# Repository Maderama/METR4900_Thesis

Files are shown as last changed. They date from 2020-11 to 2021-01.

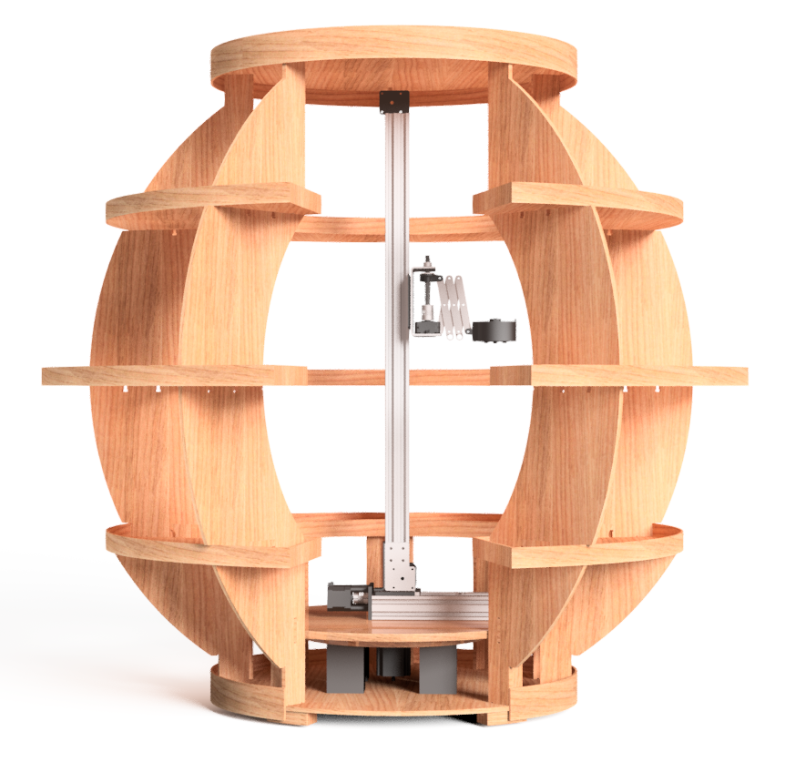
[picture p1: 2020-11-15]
CAD Model/Mechanical Drawings/Renders/FrontandSide.png

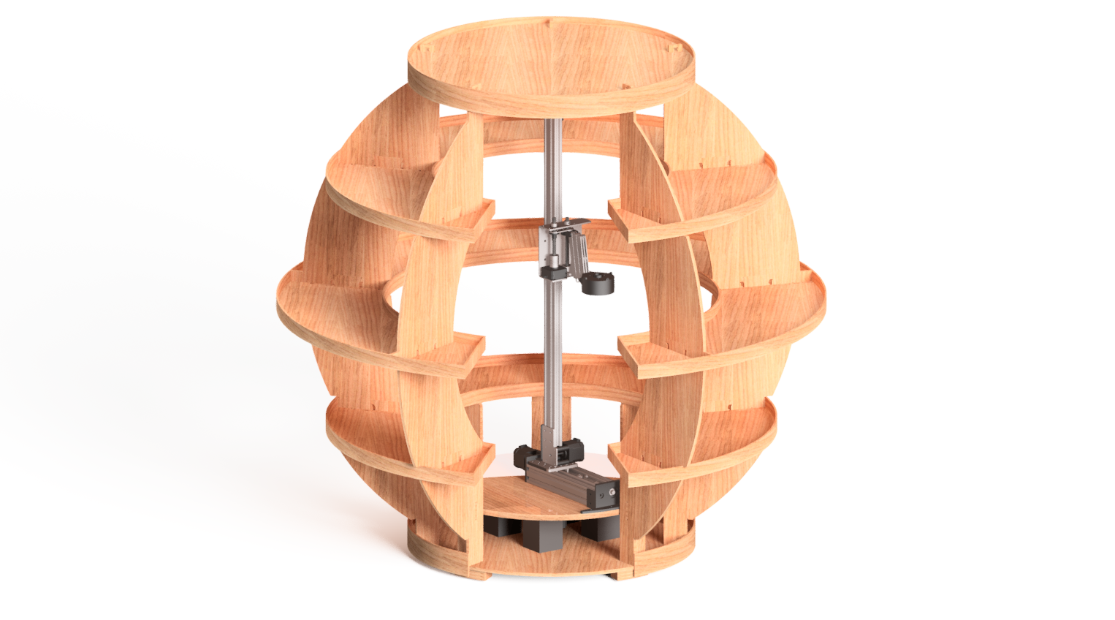
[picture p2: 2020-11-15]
CAD Model/Mechanical Drawings/Renders/GardenRender1.png

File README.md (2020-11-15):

# METR4900 FarmBot Growroom Thesis. 
This file contains all relevent material to complete this thesis. Subsequent folders have README.txt files for further information. The file structure is as follows:

## assessmentItems
This contains all assessment items completed over the year. 

## CAD Model
This contains all mechanical drawings and assembly files for the project. 

## PCB
This contains all PCB files, including the BOM.

## Software
This contains the software implementations for the project, including all source code and website code.

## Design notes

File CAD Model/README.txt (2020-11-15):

Mechanical drawings include additional renders and the full scale render aquired from Daniel Wikman. 

The FINAL folder contains the full CAD (titled full_assembly), with each subassembly located in their respective folders. 

Any missing assembly part files will be located in additionalComponents.

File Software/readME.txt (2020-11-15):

The following files contain the software implementation of the Growroom Thesis project by Madison Beare. 

theMonarch gets flashed to the arm/theMonarch PCB. 

The wemosTransmitter code gets flashed to the turntable PCB. 

To run the website, theMonarchWebsite.py will need to be modified to include the correct IP address. To run the website from the command line, a virtual workpspace was set up, and the following command run: 
python theMonarchWebsite.py. 

This assumes the correct directory has been traversed to.

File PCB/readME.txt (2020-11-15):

BOM: Total bill of materials for both PCBs
PDF: PDF outputs for schematics and 3D models
TheMonarchTransmitter: Full project files for theMonarch
WemosESP8266: Full project files for turntable

Both zipped files include all PCB files required for submission. This includes gerber files.

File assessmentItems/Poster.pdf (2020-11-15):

## KEY CHALLENGES

### 1. Support Structure of Growroom

Design must be retractable to maneuver in and around the supporting structures.

### 2. Distance Between Shelves

UTM has an approximate height of 120mm, thus height of arm must be minimized to fit between this.

### 3. Difference in Shelf Diameter

Be retractable (to clear distance d1) and extend to a distance of d2.

### 4. Size/Shape of Shelves

Restricted to a link length of D3 for any potential horizontal fold out arm (i.e. SCARA).

## DESIGN AND SOLUTION

HIGH LEVEL SOFTWARE OVERVIEW

## TOPIC & MOTIVATIONS

Australia has now been presented with an emerging opportunity for AgTech due to the following driving the changes of the agriculture industry [1]:

increasing population;

changes in demographic trends;

depleting natural resources;

climate change and;

consumer dietary demands.

Thus begs the question:
‘How can technology be used to improve and assist the agricultural sector?’

## BACKGROUND MATERIAL

GROWROOM
Many have argued that cities will need to produce food internally to respond to this demand, and as such have looked towards the vertical farm concept.

Such systems represent a paradigm shift in farming and food production and offer suitable and efficient methods for city farming by minimizing maintenance and maximizing yield [2]. Thus, the Growroom was created.

# FARMBOT GROWROOM: THE MONARCH

# Madison Beare & Dr. Matthew D’Souza

FARMBOT
The Farmbot is a current AgTech solution that uses standardized CNC machining techniques and coordinate systems to move to specific locations. The Universal
Tool Mount will
be adapted
for use in this
Thesis
application.

## TASK/AIM

To create a robotic arm for the Growroom that utilizes the UTM of the Farmbot.

THE MONARCH: FULL CAD

## FUTURE IMPROVEMENTS

Drive train/motor on turntable

Centering the motor & leadscrew

Communication protocol revisited

Website improvement/deployment

Further waterproofing

Locknut installation & purchase

## REFERENCES

[1] https://home.kpmg/content/dam/kpmg/au/pdf/2016/ powering-growth-realising-potential-agtech-australia.pdf
[2] https://www.mdpi.com/2075-5309/8/2/24/htm

3.
d2

d1

2.

1.

4.

RF Transmit (Turntable To Arm System from Webconnect)

RF Receive (Arm System from Turntable)

Arm Movement

YES

Have
coordinates
been
selected?

NO

RESET

| Angle | Reach
Closed | ≈10° | ≈0.15m
Extended | ≈45° | ≈0.29m

### 3 Axes of Movement 1. Turntable 2. C-beam/Arm 3. V-slot

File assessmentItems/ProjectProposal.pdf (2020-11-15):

# METR4900 Project Proposal

# Farmbot GrowRoom

# Madison Beare

43939442

## University of Queensland

## Semester 1, 2020

## Table of Contents

1 Project Definition | 1
2 Topic Definition | 3
3 Literature Review | 6

i

4 Progress | 9
5 Project Plan and Resources | 11
5.1.4 | Key Milestone 4: Test/Completed Deployment of Full-Scale Model . . . . 11
Appendices | 16
A GrowRoom | 17
B FarmBot Genesis Structure | 18
C FarmBot Software Overview | 19
D KUKA KR IONTEC | 20
E Preliminary Design: Extendable Arm CNC | 21
F Preliminary Design Analysis | 22

ii

## List of Figures

2.1 General Configuration of the MCU | | 4
2.2 General Coordinate System | | 4
5.1 Semester 1 2020 Project Breakdown | 12
5.2 Semester 2 2020 Project Breakdown | 12
A.1 Constructed GrowRoom | 17
A.2 Dimensioned Full-Scale GrowRoom | 17
B.1 High Level Structure Overview | 18
B.2 Structure of the FarmBot Genesis | 18
C.1 High Level Software Overview | 19
D.1 KUKA KR IONTEC Isometric View 1 | 20
D.2 KUKA KR IONTEC Isometric View 2 | 20
E.1 Cantilever 3D Printer | 21
E.2 Tiered GrowRoom Dimensions | 21

## List of Tables

1.1 Scope of Project | 2
5.1 OHS Table | 13
F.1 Ranking Descriptions | 22
F.2 Preliminary Design Rankings | 22

iii

## 1 Project Definition

### 1.1 Introduction

AgTech is the ability of digital technologies to provide the agriculture industry with the tools, data and knowledge to assist in making informed decisions to improve farming productivity and sustainability [1]. With an increasing population, changes in demographic trends, depleting natural resources, climate change and consumer dietary demands driving the change of the agriculture industry, Australia has now been presented with an emerging opportunity for AgTech. Thus begs the question: ‘How can technology be used to improve and assist the agricultural sector?’.

This project proposal will focus on the design of a robotic arm to be used in conjunction with a spherical structure (the GrowRoom) that enables individuals to grow and monitor their own food. To accomplish this, a review and analysis will be completed on past and current applications. From this, a preliminary design solution will be presented.

### 1.2 Statement of Purpose

The purpose of the FarmBot GrowRoom Project is to create and deploy a central controller that allows the application to be remotely controlled through a web portal interface [2]. More specifically, this project will focus on the design and build of a Computer Numerical Control (CNC) machine that is able to move vertically and horizontally to access plant beds in the spherical GrowRoom.

### 1.3 Goals

The goals of this project include the following:

- Design, prototype and build a 6 Degree of Freedom (DOF) robotic arm to be remotely controlled through a web portal interface;
- Create 3D CAD models of the GrowRoom and simulate movement of arm;
- Integrate the arm design with the current FarmBot Universal Tool Mount (UTM); and
- Ensure design is optimised, completed and functioning at project completion.

### 1.4 Scope

The scope of this project is outlined in Table 1.1.

Table 1.1: Scope of Project

In Scope | Out of Scope
Mechanical design of 6 DOF arm | Construction and assembly of Growroom
Electronic design considerations and build | End-effector design

Software development for arm functionality

Selection of components

Modifications to current Farmbot Universal Tool Mount (UTM)

Physical prototyping

## 2 Topic Definition

To understand the application to be designed, built and tested, relevant background information must be understood.

### 2.1 Project Description

Predictions from the Food and Agriculture Organisation of the UN (FAO) predicts that food supply will need to increase globally by approximately 60% by 2050 to sustain the estimated increase in the Earth’s population [1]. Due to this, Australia must begin to look towards the country’s ability for increased food production. This project focuses on the creation of an automated arm designed to fit inside a GrowRoom and assist in the production of crops in a more local setting and to tackle the rapidly increasing demand for more food in the future [3].

### 2.2 GrowRoom

Created by SPACE10, IKEA’s external innovation hub, the GrowRoom is the spherical structure designed to promote local food production [4]. This structure is the basis of design for the robotic arm, and the topic of this proposal. The GrowRoom structure can be seen in Appendix A.

### 2.3 CNC Components and Architecture

A CNC machine can be described as a machine that creates three dimensional objects from a solid block of material through the use of multiple carving tools [5]. For the purposes of this project, only the chassis of a CNC machine will be replicated. That is, the standard end-effector (usually comprised of a mill, drill or lathe tool component) will not be required. For replication purposes, the main components of a CNC machine have been identified.

### 2.3.1 CNC Software

The controller/computer in a CNC machine are generally operated by means of three types of software programs. These can be described as the operating system software, machine interface software, and application software [6]. The primary function of the operating system is to drive the machine tool axes by generating and handling control signals, while the machine interface software acts as a communication link between the central processing unit (CPU) and the machine tool axes [6]. The application software dictates the position of the end-effector relative to the workspace provided.

### 2.3.1.1 Geometric Code (G-Code)

G-code is the most common CNC programming language that instructs machines where and how to move. To ensure the accurate movement of the system, transnational performance is described in three simple ways [7]:

1. Rapid move: linear movement to an XYZ position at the fastest speed possible.
2. Feed move: linear movement to an XYZ position at a specified rate.
3. Circular move: circular movement at a specified rate.

G-Code follows some variation of an alphanumeric code that are used as a simple way to define motion, declare a position, set a value, select an item and dictate power mode (i.e. on/off) [7].

### 2.3.2 Machine Control Unit (MCU)

A machine control unit (MCU) is a computer with related hardware that executes programs/instructions by converting each command into specific actions of the processing equipment [6]. A general configuration of this control unit is shown in Figure 2.1.

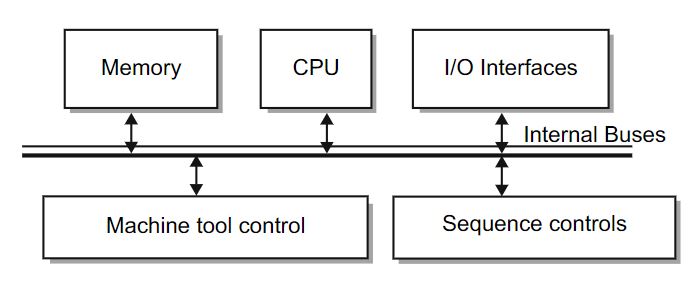
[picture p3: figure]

Figure 2.1: General Configuration of the MCU

Source: [5]

Each of these contributes to the effective motion of axes through reception and interpretation of translated data.

### 2.3.3 Drive System

Basic functionality of a CNC machine includes the requirement for automatic, precise and consistent movement [6]. A general co-ordinate system comprising of a standard axis must be used to define the position of the end-effector relative to the workspace to ensure driving system accuracy.

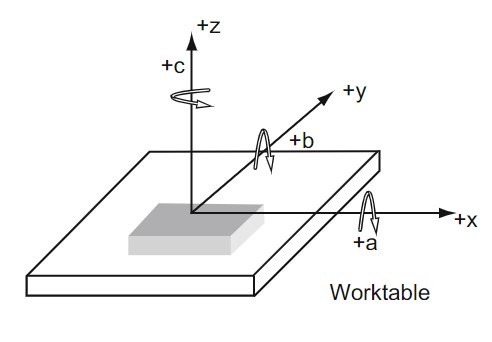
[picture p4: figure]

Figure 2.2: General Coordinate System

Source: [5]

This system generally comprises of three linear axes (x, y, z) in the Cartesian coordinate system, plus three rotational axes (a, b, c) as shown in Figure 2.2.

Two common transmission systems to drive linear axes of a CNC controller can be comprised of either leadscrews or belts and pulleys - both powered by motors.

### 2.3.3.1 Leadscrew Transmission

A leadscrew is a threaded rod that turns rotational motion into linear motion. Transmission systems that make use of these rigid, threaded rods are designed to be accurate, strong and reliable [8]. Due to the high repeatability and accuracy, little ongoing maintenance is required.

### 2.3.3.2 Belt and Pulley Transmission

A belt and pulley CNC machine is commonly seen in 3D printer designs, and are significantly lighter than leadscrew transmission systems [8]. Not limited by size/length, a belt and pulley system can be fixed around a rolling wheel or fitted over gears if required.

### 2.3.4 Feedback System

Feedback systems relay data and information specifications during and after a process is completed [9]. Feedback devices include linear transducers, limit switches, direct position scales and linear/rotational encoders. Each of these devices aims to detect/monitor the presence of an object to indicate whether the movement limits of that object have been exceeded [10].

## 3 Literature Review

This section will outline and summarise existing works and developed applications with similarities to this project.

### 3.1 FarmBot

### 3.1.1 Overview

FarmBot is an open-source, automated CNC farming machine [11]. The CNC farming machine consists of a Cartesian co-ordinate, gantry style robotic system. FarmBot is capable of movement in the x,y and z planes.

There are two different models of FarmBot - FarmBot Express and FarmBot Genesis. FarmBot Express has been made to accommodate affordability and ease of construction, while FarmBot Genesis offers enhanced capabilities with advanced features and is able to service larger areas [12].

The core components of FarmBot Genesis are detailed below.

### 3.1.2 Hardware

### 3.1.2.1 Structure

Appendix B Figure B.1 gives a basic overview to the structure of FarmBot genesis, in relation to a specified workspace. From this, it is clear that x, y and z plane movement are governed through different physical structures.

Tracks allow the FarmBot genesis to move along the x-axis. These tracks are composed of 1.5m long aluminium extrusions, positioned end-to-end to allow for track lengths of 3m, 6m and 18m, depending on the size of the ordered kit [13].

The FarmBot gantry structure is comprised of linear guides created from V-slot aluminum extrusions and V-wheels from Open Builds [14]. This gantry rigidly bridges the tracks, spanning in across the y axis. These linear guides are incorporated with aluminium alloy plates and brackets, as well as ABS plastic components to assemble the FarmBot Genesis Structure shown in Appendix B Figure B.2.

The cross-slide moves along the y-axis (the fixed gantry). This serves as the base for the z-axis to attach to while the Universal Tool Mount is attached to the z-axis.

### 3.1.2.2 Transmission System

The FarmBot Genesis drive-train consists of four NEMA 17 stepper motors with rotary encoders. These allow for x, y and z translation. GT2 timing belts and pulley are directly attached to the stepper motors/driveshafts and assist in movement in the x and y directions. A stainless steel precision leadscrew (8mm ACME) is used to allow movement in the z direction [15].

### 3.1.3 Electronics

A Raspberry Pi 3 is used as the “host computer” of FarmBot [16]. This runs FarmBot operating system, communicates with the web application over ethernet or WiFi, and communicates to the Farmduino over a USB serial connection [16].

A ’Farmduino’ is a customised electronics board that incorporates the functionality of a microcontroller (MEGA 2560) and a Reprap Arduino Mega Pololu Shield (RAMPS) shield [16]. This integrates with the stepper motors and monitors information from feedback devices whilst receiving commands from the Raspberry Pi.

### 3.1.4 Software

The FarmBot software system is comprised of external resources, the FarmBot web application, the user, and the FarmBot device [17]. Each component will be outlined below, with a high level overview shown in Appendix C.

### 3.1.4.1 FarmBot Cloud Services

FarmBot Web Application
The FarmBot web application allows for control and configuration of the Farmbot through smart devices [17]. This application includes features such as drag and drop farming and the graphical design of the garden to user specification.

Message Broker
This is a cloud application that acts an an intermediary between the external resources, the web application, the user and the FarmBot device. Socket connections, device identification and authentication are handled through this intermediary medium [17].

### 3.1.4.2 Device Software

FarmBot Operating System
A Raspberry Pi runs a custom operating system for the FarmBot to interact with the web application via the message broker [17]. This allows events to be controlled in real time. This operating system communicates with the Farmduino/Arduino to send G and F code commands and also receives and collects data from feedback systems [17].

Arduino Firmware
The firmware of the system is uploaded onto the Arduino/microcontroller and is used to configure and control stepper motors and rotary encoders, tools and peripherals, sensors and other electronic components. It receives G-Code commands and sends collected data from feedback systems to the Raspberry Pi.

### 3.1.5 Universal Tool Mount (UTM)

The UTM is a plastic component mounted to the z-axis that allows for the switching between different tools to complete tasks. This is the end-effector of the system and includes multiple piping connections/passageways for water, fertiliser and air to pass through [18].

### 3.2 KUKA

### 3.2.1 Overview

KUKA is one of the world’s leading suppliers of intelligent automation solutions, and this includes applications of robotics, automation, logistics and electronics [19].

The KR IONTEC 6 DOF robot designed and manufactured by KUKA is shown in Appendix
D. This robot arm is one of the newest applications, and has the desired reach for the proposed system.

The KR IONTEC has a payload of approximately 30-50kg depending on the model, and has a reach of up to 2100 - 2500mm [20]. For the purposes of this project, a no payload is required, however a reach of approximately 2500mm or greater is desired.

The KR IONTEC is equipped with both waterproof and dust-proof protected motors and its application is not limited to one area.In relevance to this project, KUKA.CNC has been researched to identify how a CNC application can be applied to a system that does not follow the standard CNC system/build.

### 3.2.2 KUKA.CNC

KUKA.CNC is a software system that can be linked to KUKA robots and allow them to be operated like a conventional CNC controller. This allows for CNC-based robot programming, improved robot path performance and offline programming options via CAD/CAM system [21].

To allow this operation, a Numerical Controller (NC) has been incorporated into the KR C4
- a controller/control system that incorporates robot control, programmable logic controller (PLC) control, motion control and safety control [22].

The KUKA.CNC option allows for KUKA robots to operate via G-Code. It can process complex programs from CAD/CAM systems due to CNC path planning and thus can integrate robots to play a direct role in the machining process [22].

The user interface of the KUKA.CNC allows for users to execute G-Code commands and CAD/CAM simulation without having to compile them into the robot language [21]

## 4 Progress

This section will detail the preliminary design of the arm, and current progress completed. It has been decided that a smaller scale GrowRoom (dimensions: height - 0.8m, diameter -0.85m, ring spacing 0.2m) and arm will be designed and executed before a larger scale model is deployed.

The preliminary designs have been completed will the full-scale model in mind, under the assumption that any/all specifications met for the large scale design will be met for the small scale implementation.

### 4.1 Preliminary Design/s

There are three initial designs that have been considered potential solutions. These are outlined in the following subsections.

### 4.1.1 Extendable Arm CNC

This design features a design similar to a cantilevered 3D printer - this can be seen in Figure E.1 Appendix E. This design would incorporate much of the FarmBot mechanical components, and creates an inverted L-shaped arm. Difficulties associated with this is that the cantilevered arm must have an extension of some sort to be able to reach each planter box, as the edge of each is a different distance from the center (as the design tiers - shown in Figure E.2 Appendix
E. The arm must also be able to move in and around the supporting structures that separate each box. This may require counterweight calculations to ensure the design is capable of the required extension. This design is fixed onto the bottom of the GrowRoom on a turntable device that allows the arm to rotate 360 degrees if required.

### 4.1.2 Multiple Extendable Arm CNC

This design mirrors the above cantilevered 3D design, with an arm at each tiered level of planter bed. Due to the dividers between the beds, this design would still need to incorporate an arm that is able to move/extend to reach the outer diameter of the boxes. This design means that arms can be fixed at each level and do not need to translate up and down the central arm. This design would keep the turntable as it’s form of rotation. Although this reduces one axis of movement (by having fixed arms at each level), this design is also more complex in terms of setup, will require more components (more motors, electrical components, UTM’s etc.) that may cause the design to become too mechanically complex.

4.1.3 6 Degree of Freedom Robot Arm

A KUKA 6 DOF robot arm can be seen in Appendix D. A design similar to this will require more calculation in terms of working out specific arm, shoulder and wrist lengths, and determining the inverse kinematics of the design to ensure it is possible to reach each planter bed. This design will not require any extendable mechanical parts, but will require extreme precision and potential complexity in terms of coding implementation. As the scale of this project is also large (approximately 2.5 meters fully extended) the arm lengths and subsequent torque requirements of motors may require components that are too expensive to be feasible.

### 4.2 Analysis and Feasibility

To determine the feasibility of each design, a decision matrix was created with the criteria of cost, design/build complexity and size. Before completing this, the following assumptions were made:

1. The multiple extendable arm (option 2) is approximately five times as expensive as the extendable arm option (option 1). This is because there will be five arms as opposed to one.
2. The 6 Degree of Freedom Robot Arm will be created from machined components.

Appendix F Tables F.1 and F.2 show the ranking parameters and the final rankings for each of the preliminary designs. As shown, the preliminary design with the lowest - and therefore most desirable - ranking is the Extendable Arm CNC. As each of the criteria were deemed equal in weighting, this design was chosen due to its potential low cost and size. From here, both this design and the 6 DOF robot arm should be developed further (as their rankings were extremely close) to determine which design is more feasible.

## 5 Project Plan and Resources

### 5.1 Key Milestones

The success of the project will ultimately be governed by the arm capability upon deployment. In order to achieve this outcome, milestones must be met along the project duration. These are outlined below.

### 5.1.1 Key Milestone 1: Design Finalisation

Date/s: 24/02/2020 - 13/04/2020
Resources: internet, research papers, CAD software.
Description: The preliminary design has been completed, and relevant adjustments made. All design choices have been justified and confirmed by theoretical calculations.

### 5.1.2 Key Milestone 2: Project Seminar

Date/s: 18/05/2020 - 22/05/2020
Resources: Internet, research papers, PCB software, CAD software, microcontroller software. Description: This will be a presentation on the finalised design, with a full Computer-Aided Design (CAD) model completed. At this stage, all progress will be reported on and the theoretical design will be presented.

### 5.1.3 Key Milestone 3: Miniature Prototype Executed

Date/s: 03/08/2020 - 10/08/2020
Resources: Oscilloscope, general electronic components, microcontroller, motors, breadboards, hardware components, PCB manufacturer, power supply.
Description: The miniature prototype has been deployed, and any errors and areas of improvement have been identified. At this stage, changes are able to be made before the build and deployment of the full-scale model.

### 5.1.4 Key Milestone 4: Test/Completed Deployment of Full-Scale Model

Date/s: 05/10/2020 - 12/10/2020
Resources: All completed mechanical and electrical components.
. Description: A test of the full-scale model will occur. Any errors or areas of improvement will be identified for change before the final deployment occurs. Final demonstration will occur in both the thesis demonstration and the trade show.

### 5.1.5 Key Milestone 5: Thesis

Date/s: 19/10/2020 - 09/11/2020
Resources: Internet, final design and research completed.
Description: The final thesis will comprise of all research and design completed throughout the year. It will include a report detailing all progress completed and findings.

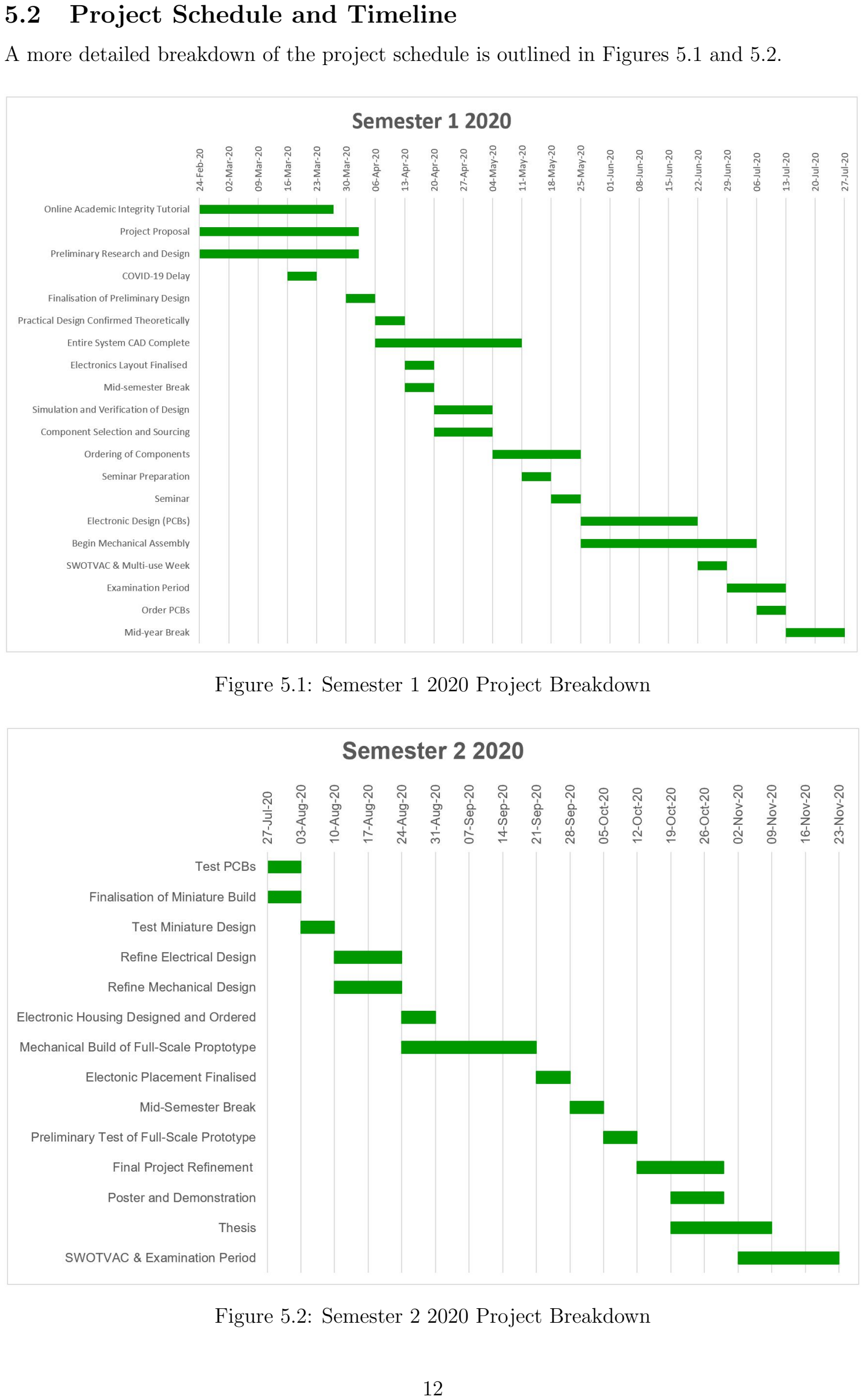
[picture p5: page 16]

### 5.2 Project Schedule and Timeline

A more detailed breakdown of the project schedule is outlined in Figures 5.1 and 5.2.

Figure 5.1: Semester 1 2020 Project Breakdown

Figure 5.2: Semester 2 2020 Project Breakdown

### 5.3 OHS Risk Assessment

The Robotics Design Studio (50-C406) is a high risk laboratory, and the Electrical Engineering Project Laboratory (50-S105) is a low risk laboratory. OHS Laboratory Rules and Requirements have been completed to gain access to these labs, with Table 5.1 outlining the risks associated with completing the project in these locations.

Table 5.1: OHS Table

Hazard | Description | Risk Level | Mitigation Strategy
Electrical | Danger of elec-trocution due to electrical equip-ment malfunction | Medium | Ensure all electrical equipment is tagged and tested, no loose or fraying wires are present. Re-port all/any damaged equipment to supervisor.
Environmental | Slips, Trips and Falls | Low | Ensure all walk-ways are clear, and any spills are cleaned imme-diately.
Electrical | Burns due to com-ponent overheating or soldering | Medium | Keep hands clear of soldering irons at all times and turn power off to overheated components. Run burned area under cold wa-ter and seek further assistance if necessary
Environmental | Hazardous fumes from soldering | Low | Wear Personal Protective Equip-ment (PPE) when required, en-sure soldering fans are on at all times.
Electrical | Danger of electro-cution due to con-tact with water | Low | Ensure all components are water-proofed and care is taken when opening potentially wet compo-nent casings. Ensure all power is turned off prior.
Physical | Physical abrasions due to mechanical equipment (cuts, scratches, scrapes) | Medium | Ensure all cuts are made away from the body, take care when handling equipment and tools. Bandage area if need be, and seek further assistance if required.

## Bibliography

[1] A. | Goddard, | S. | Bird, | B. | Van | Delden, | A. | McCauley, | and | A. | Gruszka.
(2016) | Powering | Growth: | Realising | the | potential | of | AgTech | for | Aus-
tralia. | [Online]. | Available: | https://home.kpmg/content/dam/kpmg/au/pdf/2016/
powering-growth-realising-potential-agtech-australia.pdf
[2] M. D’Souza. (2019, Dec.) Embedded Systems Super Thesis Project: Farmbot GrowRoom. [Online]. Available: https://student.eait.uq.edu.au/projects/?act=project detail\&id= 5071
[3] SPACE10. (2014, Feb.) Space10 open sources The Growroom. [Online]. Available: https://medium.com/space10/space10-open-sources-the-growroom-aa7ca6621715
[4] P. | Stephens. | (2017, | Feb.) the | growroom: | IKEA’s | innovation | lab | open
sources flat-pack garden. [Online]. Available: | https://www.designboom.com/design/
ikea-space10-the-growroom-flat-pack-spherical-garden-02-20-2017/
[5] P. Hood-Daniel and J. Kelly, Build Your Own CNC Machine. Apress, 2009. [Online]. Available: https://link-springer-com.ezproxy.library.uq.edu.au/content/pdf/10. 1007%2F978-1-4302-2490-7.pdf
[6] P. Zhang, Advanced Industrial Control Technology. Elsevier Inc., 2010. [Online]. Available: https://www.sciencedirect.com/science/article/pii/B9781437778076100075
[7] Autodesk. (2020) Getting Started with G-Code. Autodesk. [Online]. Available: https: //www.autodesk.com/industry/manufacturing/resources/manufacturing-engineer/g-code
[8] Maker Store Team. (2014) DIY CNC Machines and Components. Maker Store. [Online]. Available: https://www.makerstore.com.au/blog/diy-cnc-machines-and-components/
[9] Tool | & | Machine | LTD. | (2017, | Jan.) | Components | of | a | CNC | machin-
ing system. Tool & Machine LTD. [Online]. Available: | https://rwdtool.com/
components-of-a-cnc-machining-system/blog.html
[10] T. P. Company. (2020) Limit Switch Characteristics. [Online]. Available: https: //www.thomasnet.com/articles/instruments-controls/limit-switches/
[11] R. Aronson. (2016, Oct.) The Farmbot Project. [Online]. Available: http://wiki.farmbot.org/the-farmbot-project?rev=1476254909
[12] FarmBot. (2020) Which FarmBot is right for you? [Online]. Available: https://farm.bot/
[13] ——. (2020, Mar.) Tracks. [Online]. Available: https://genesis.farm.bot/docs/tracks
[14] R. Aronson. (2014, Aug.) Project Details For FarmBot - Open-Source CNC Farming. [Online]. Available: https://hackaday.io/project/2552-farmbot-open-source-cnc-farming/detailshttps://hackaday.io/project/2552-farmbot-open-source-cnc-farming/details
[15] FarmBot. (2019) Drivetrain. [Online]. Available: https://genesis.farm.bot/docs/drivetrain

[16] ——. (2019, Mar.) Electronics and Wiring. [Online]. Available: https://genesis.farm.bot/docs/electronics-and-wiring
[17] ——. (2019, Jul.) Software High Level Overview. FarmBot. [Online]. Available: https://software.farm.bot/docs
[18] ——. (2019, Dec.) Universal Tool Mount. [Online]. Available: https://genesis.farm.bot/docs/utm
[19] K. AG. (2020) About Page. [Online]. Available: https://www.kuka.com/en-au/about-kuka
[20] KUKA. (2020) KR IONTEC. [Online]. Available: https://www.kuka.com/en-au/products/robotics-systems/industrial-robots/kr-iontec#Brochure
[21] ——. (2020) KUKA.CNC. [Online]. Available: https://www.kuka.com/en-au/products/robotics-systems/software/application-software/kuka cnc
[22] ——. (2020) KUKA KR C4: | The Power of Control. [Online]. Available: | https:
//www.kuka.com/en-au/products/robotics-systems/robot-controllers/kr-c4
[23] D. Friis. (2017, | Mar.) Open Source Growroom Dimensions. [Online]. Avail-
able: | https://github.com/space10-community/the-growroom/blob/master/dimensions
open source growroom.pdf
[24] FarmBot. (2020, Feb.) FarmBot Genesis High Level Overview. [Online]. Available: https://genesis.farm.bot/docs/high-level-overview
[25] S. Lowe. (2016, Jun.) Cartesian Style Bots. [Online]. Available: https://openbuilds.com/builds/makersl-msl-5-cantilevered-3d-printer.3179/
[26] D. Wikman, Drawing, Mar. 2020.
[27] J. | Chandler | and | J. | Herriot, | “EAIT | Workshop | AEB,”
Jun. | 2019. | [Online]. | Available: | https://docs.google.com/spreadsheets/d/
1tGXx3zWUWgfRmiD8zYq74hc8V-P3EETRn3JgAiONnQY/edit?usp=sharing

# Appendices

## A GrowRoom

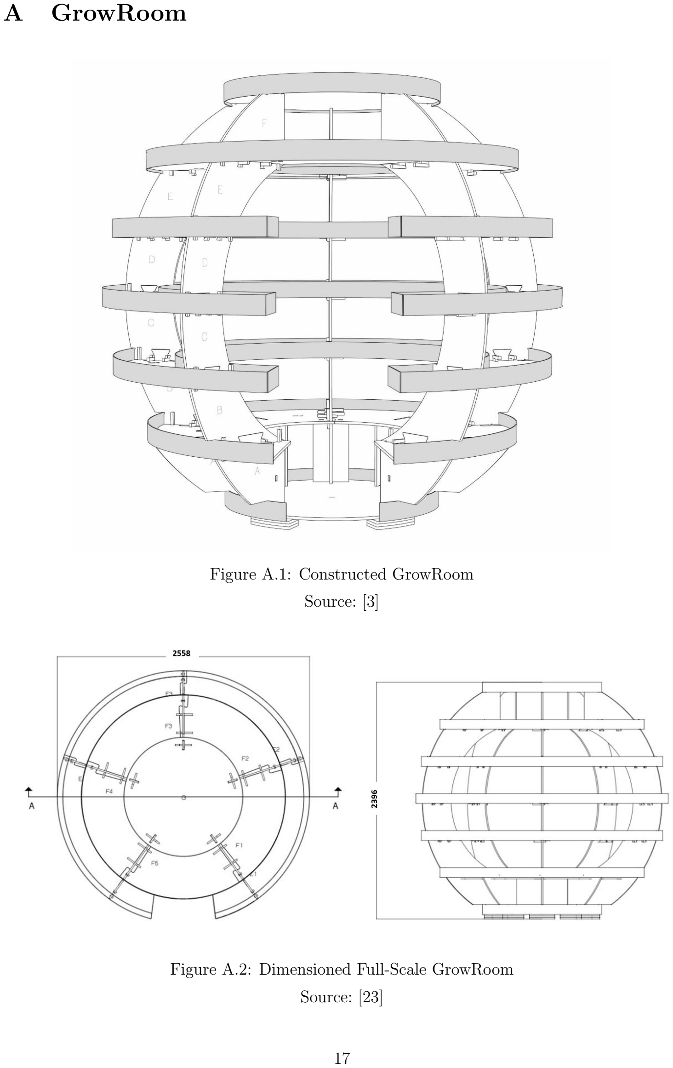
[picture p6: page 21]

Figure A.1: Constructed GrowRoom

Source: [3]

Figure A.2: Dimensioned Full-Scale GrowRoom

Source: [23]

## B FarmBot Genesis Structure

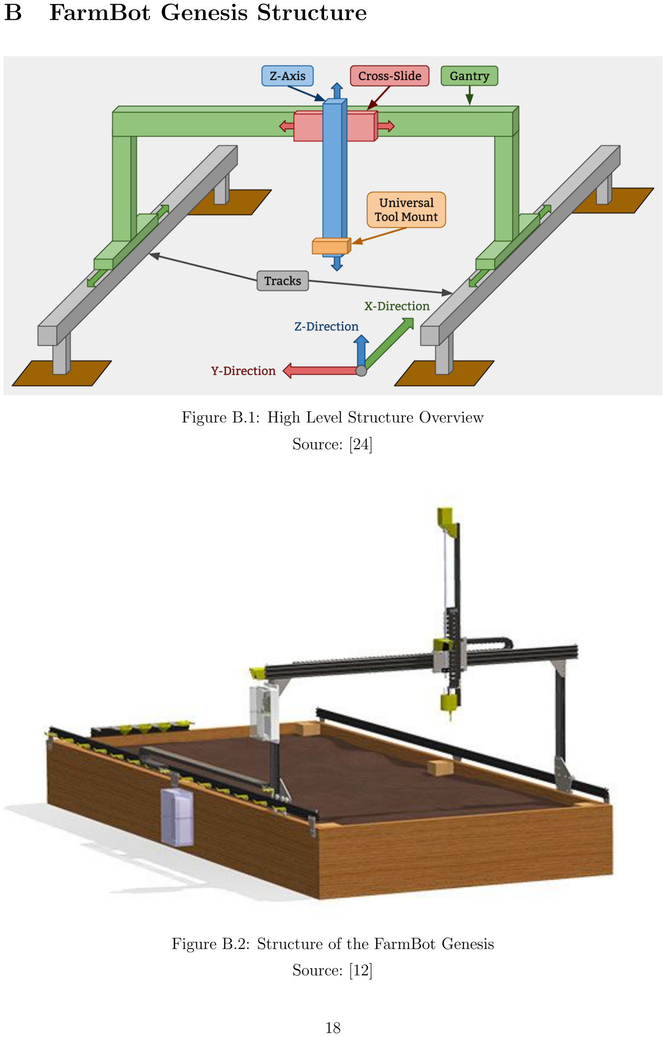
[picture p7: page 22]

Figure B.1: High Level Structure Overview

Source: [24]

Figure B.2: Structure of the FarmBot Genesis

Source: [12]

## C FarmBot Software Overview

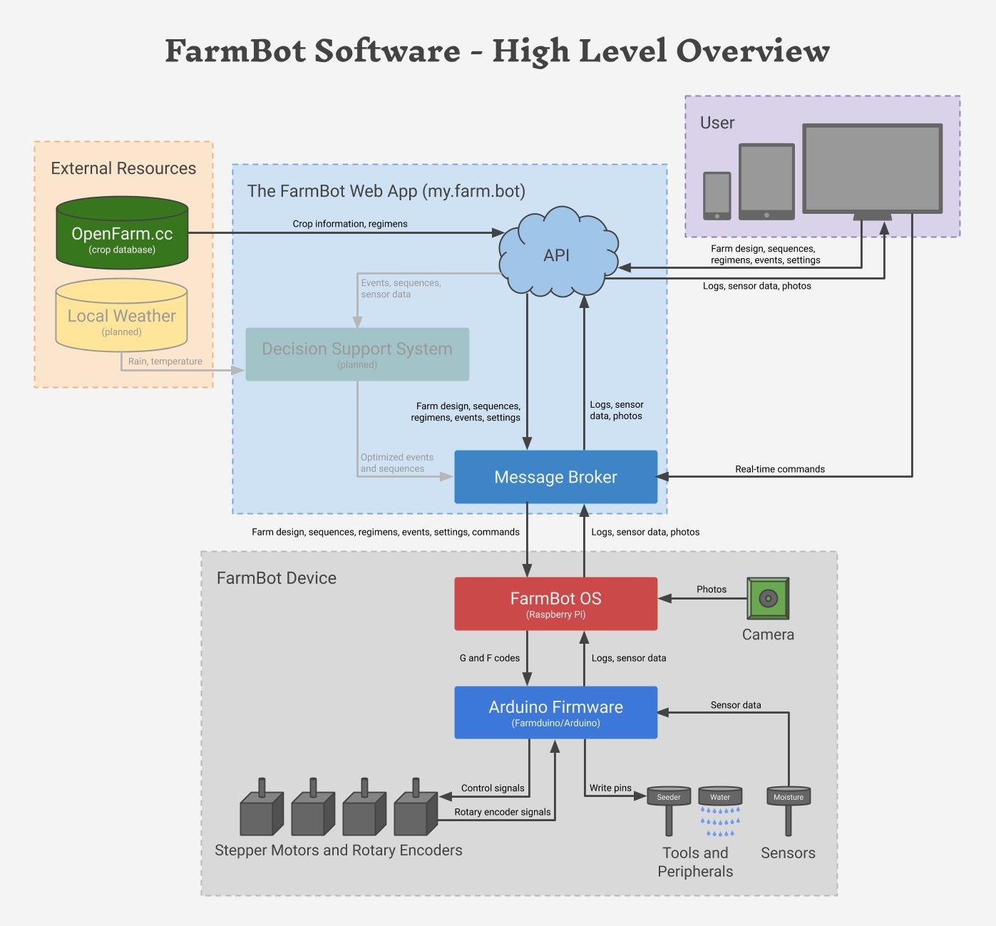
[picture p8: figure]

Figure C.1: High Level Software Overview

Source: [17]

## D KUKA KR IONTEC

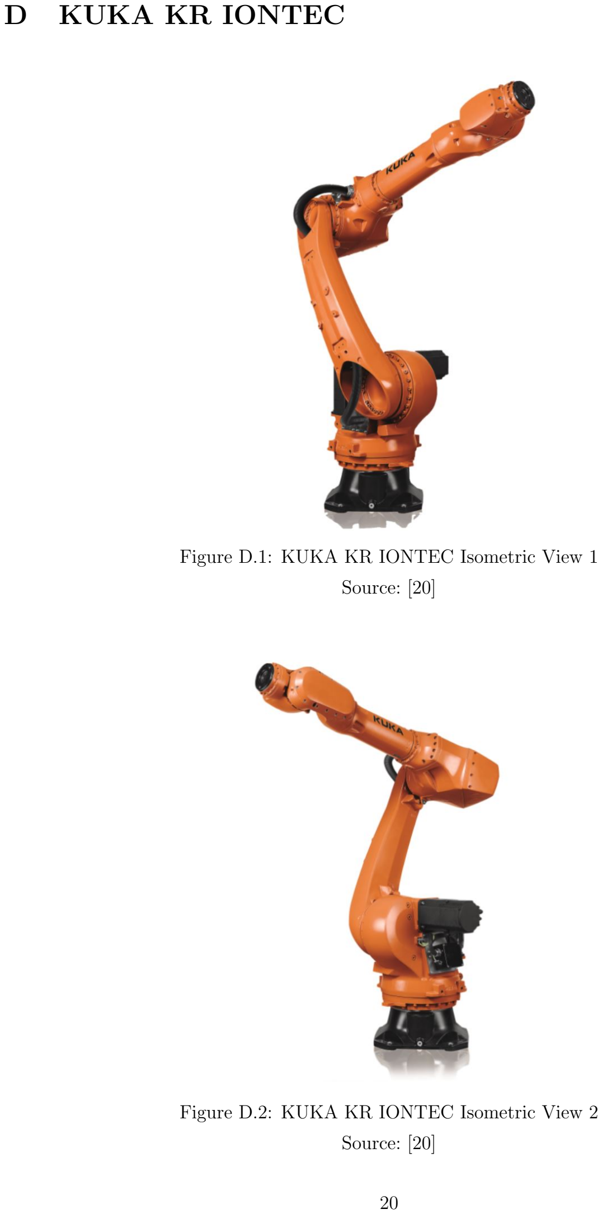
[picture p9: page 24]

Figure D.1: KUKA KR IONTEC Isometric View 1

Source: [20]

Figure D.2: KUKA KR IONTEC Isometric View 2

Source: [20]

## E Preliminary Design: Extendable Arm CNC

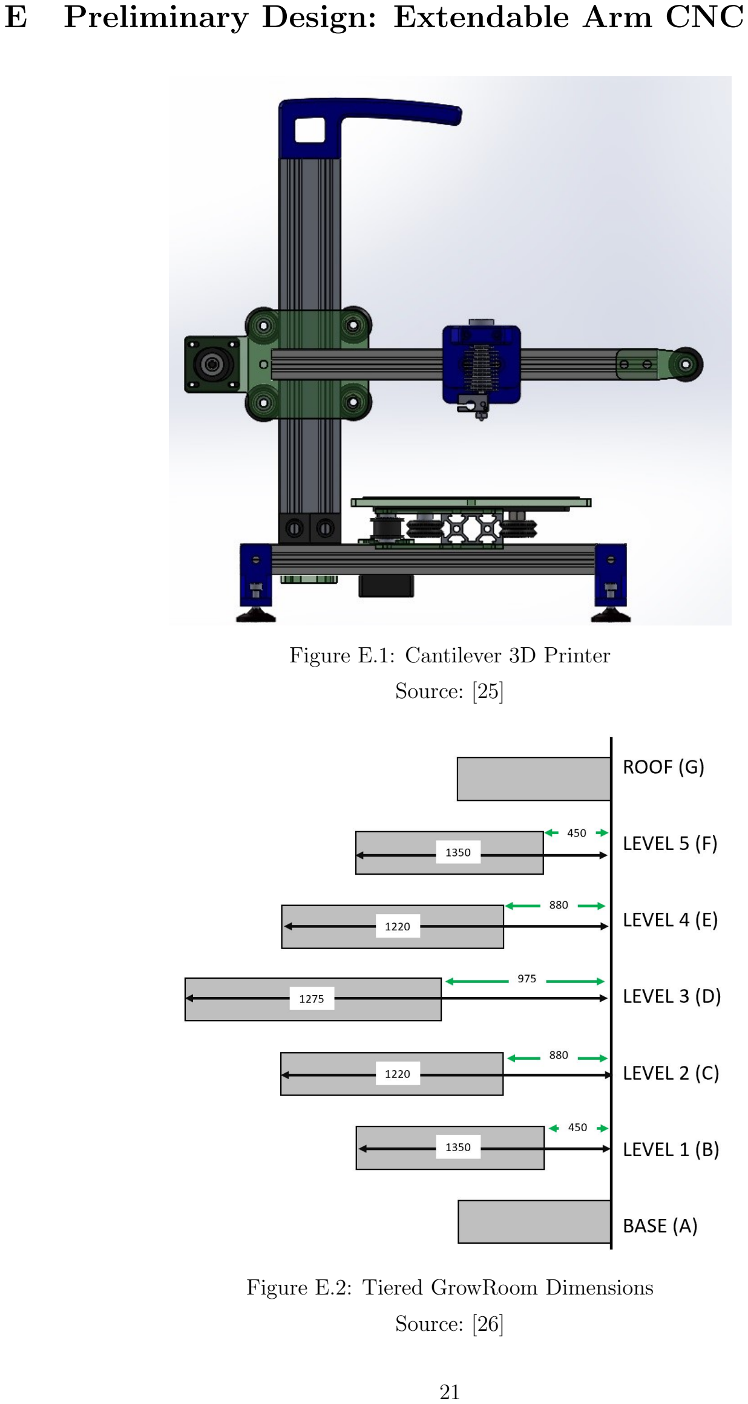
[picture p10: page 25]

Figure E.1: Cantilever 3D Printer

Source: [25]

Figure E.2: Tiered GrowRoom Dimensions

Source: [26]

## F Preliminary Design Analysis

Table F.1: Ranking Descriptions

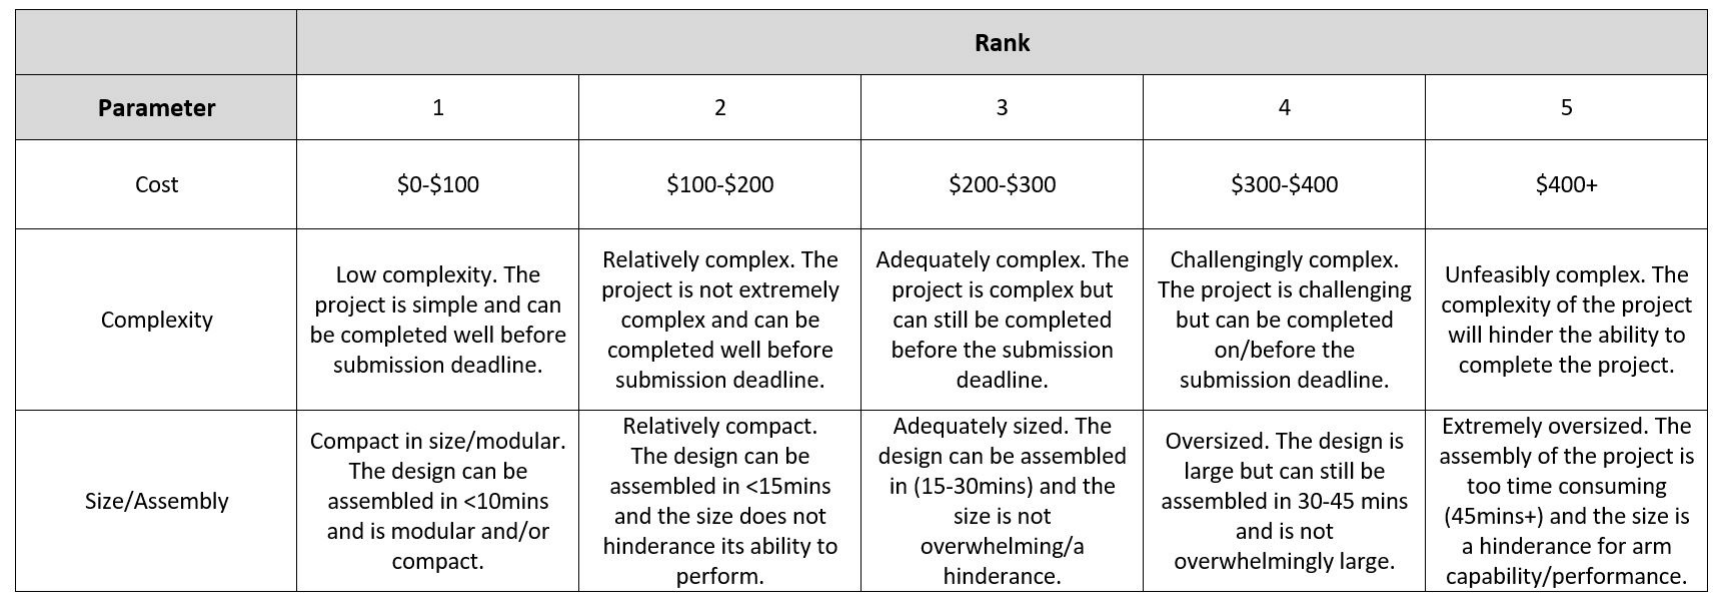
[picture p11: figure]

Table F.2: Preliminary Design Rankings

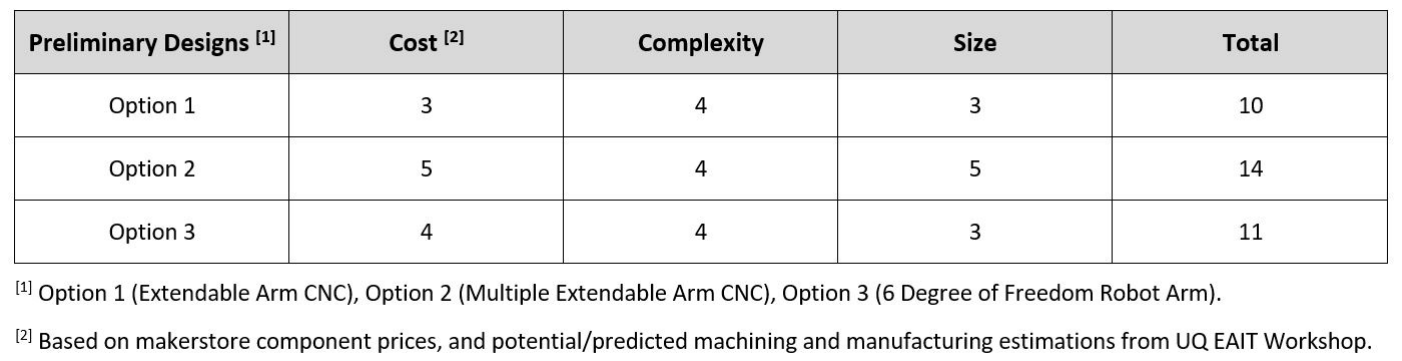
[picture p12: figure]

Source: [8], [27]

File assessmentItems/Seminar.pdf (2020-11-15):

# FARMBOT GROWROOM

# Madison Beare

## METR4900 Semester 1, 2020

43939442

## Supervisor: Matthew D’Souza

# PRESENTATION CONTENTS

▣ Thesis introduction, scope and relevance;

▣ Background information and literature review;

# ▣ Work completed so far and

▣ Work remaining to be done.

# INTRODUCTION, SCOPE AND RELEVANCE

## Why is this project important?

# INTRODUCTION: RELEVANCE

▣ AgTech is the collection of digital technologies that provide the agricultural industry with the tools, data and knowledge to make more informed and timely on-farm decisions [1]
▣ Changes driving the agriculture industry:
- increasing population;
- changes in demographic trends;
- depleting natural resources;
- climate change and
- consumer dietary demands.
▣ Thus begs the question:
‘How can technology be used to improve and assist the agricultural sector?’

# INTRODUCTION, SCOPE

▣ This project will focus on the design of a robotic arm to be used in conjunction with a small scale spherical structure (the GrowRoom) that enables individuals to grow and monitor their own food.

In Scope | Out of Scope
Mechanical design | Construction and assembly of GrowRoom
Electronic design and build | End-effector design
Software development
Component selection
Modifications to current Farmbot Universal Tool Mount (UTM)

Physical prototyping

# LITERATURE REVIEW

## Background information and past works

# LITERATURE REVIEW: GROWROOM

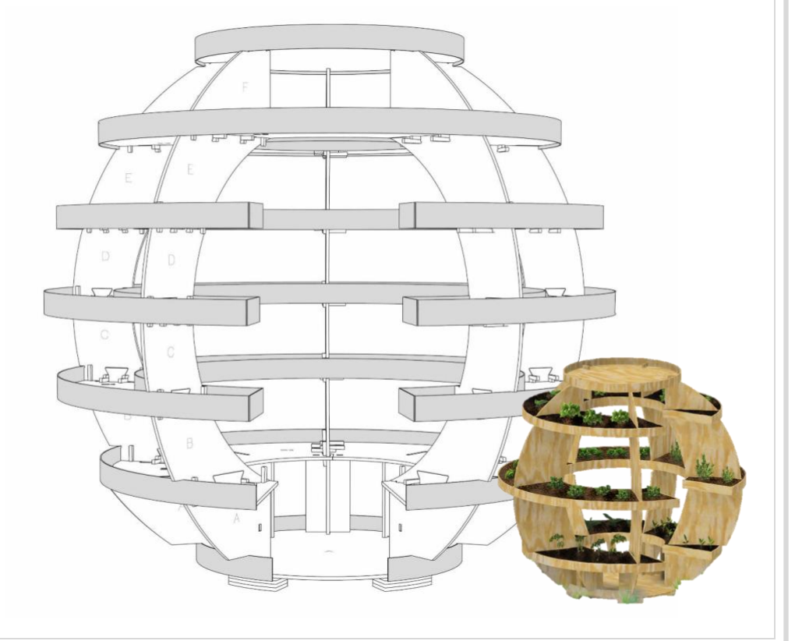
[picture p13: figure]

▣ Created by SPACE10, IKEA’s external innovation hub, the GrowRoom is the spherical structure designed to promote local food production.

▣ This project will focus primarily on the design and build of a robotic arm to fit inside a small scale (approximately 0.8m x 0.5m x 0.5m GrowRoom).

# LITERATURE REVIEW: FARMBOT

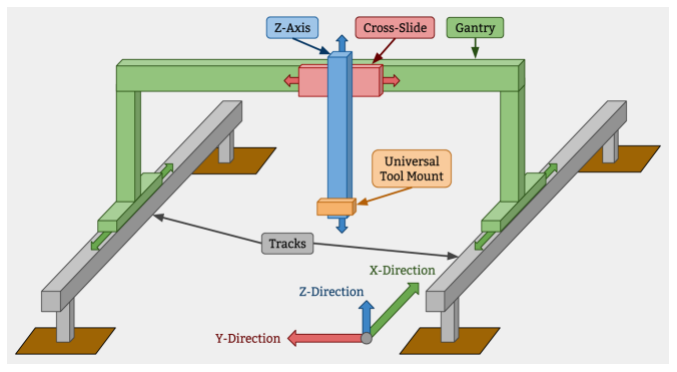
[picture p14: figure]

HARDWARE
▣ The CNC farming machine consists of a Cartesian co-ordinate, gantry style robotic system.
▣ FarmBot is capable of movement in the x,y and z planes, governed through different physical structures:
- Tracks (x direction)
- Gantry (y direction)
- Lead Screw (z direction)

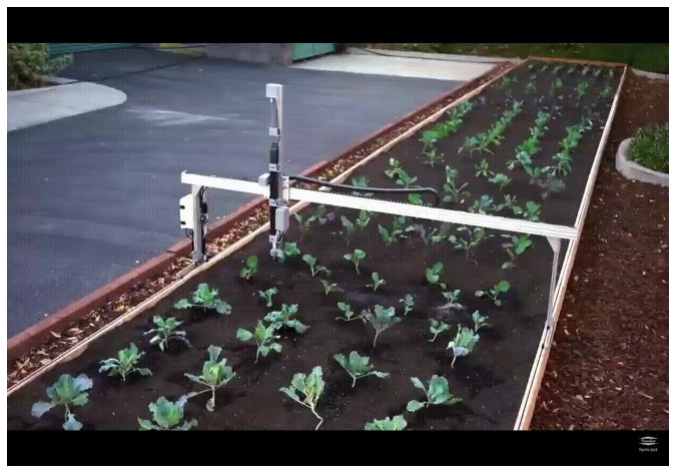
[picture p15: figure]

SOFTWARE
▣ A Raspberry Pi 3 is used as the “host computer” of FarmBot [16]. ▣ This:
- Runs the operating system
- Communicates with the web application over ethernet or Wi-Fi.
- Communicates to the
Farmduino over a USB serial connection.

ELECTRICAL
▣ “The ’Farmduino’ is an electronics
board | that | combines | the
functionality of an Arduino MEGA 2560 microcontroller and a RAMPS shield” [16].
▣ It:
- Integrates with stepper motors and monitors information.
- Receives commands from the Raspberry Pi.

# LITERATURE REVIEW: SCARA

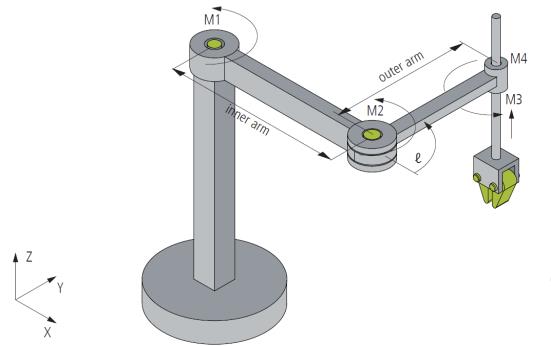
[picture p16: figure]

### ▣ SCARA is an acronym for Selective Compliance

Articulated Robot Arm.

### - Compliant in the X-Y axis, and rigid in the Z-

axis.

### ▣ The SCARA’s structure consists of two arms joined at

the base and the intersection of arms one and two.

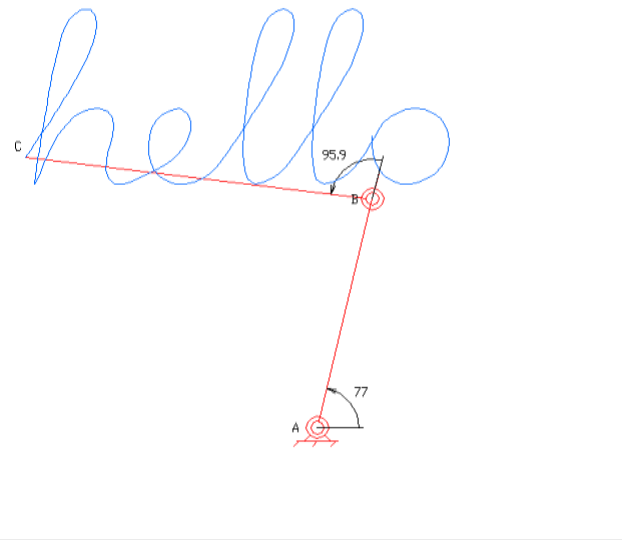
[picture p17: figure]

### ▣ The final X-Y location at the end of arm two is a factor of the M1 angle, M2 angle, length of arm one and

length of arm two.

▣ SCARAs are four-axis robots.

# CURRENT PROGRESS

## What has been done so far?

# KEY CHALLENGES

## 1. The support structure of the

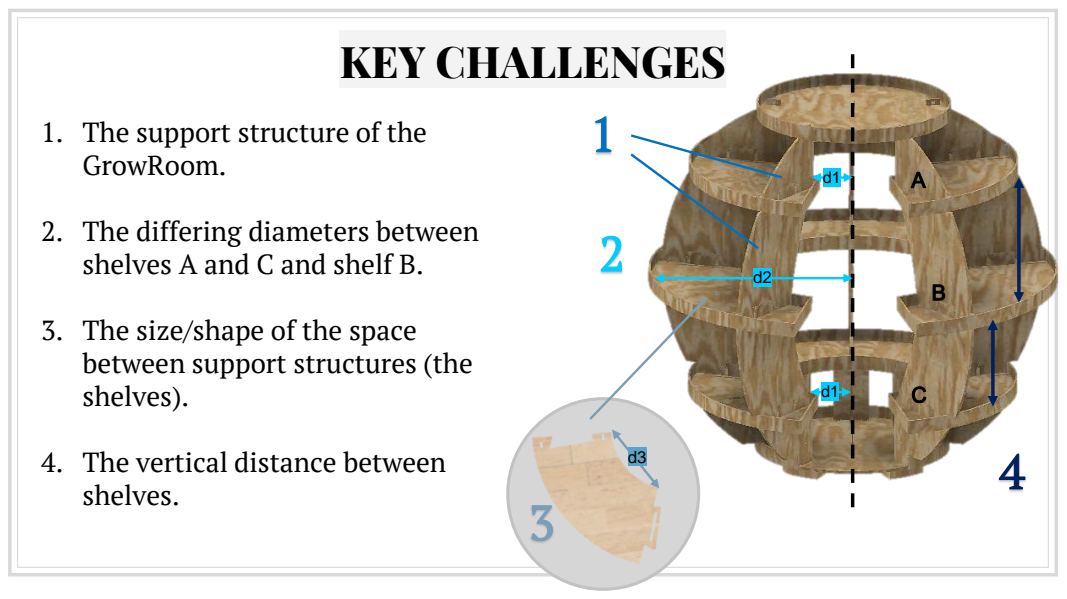
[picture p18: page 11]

GrowRoom.
2. The differing diameters between
shelves A and C and shelf B.
3. The size/shape of the space
between support structures (the
shelves).
4. The vertical distance between
shelves.

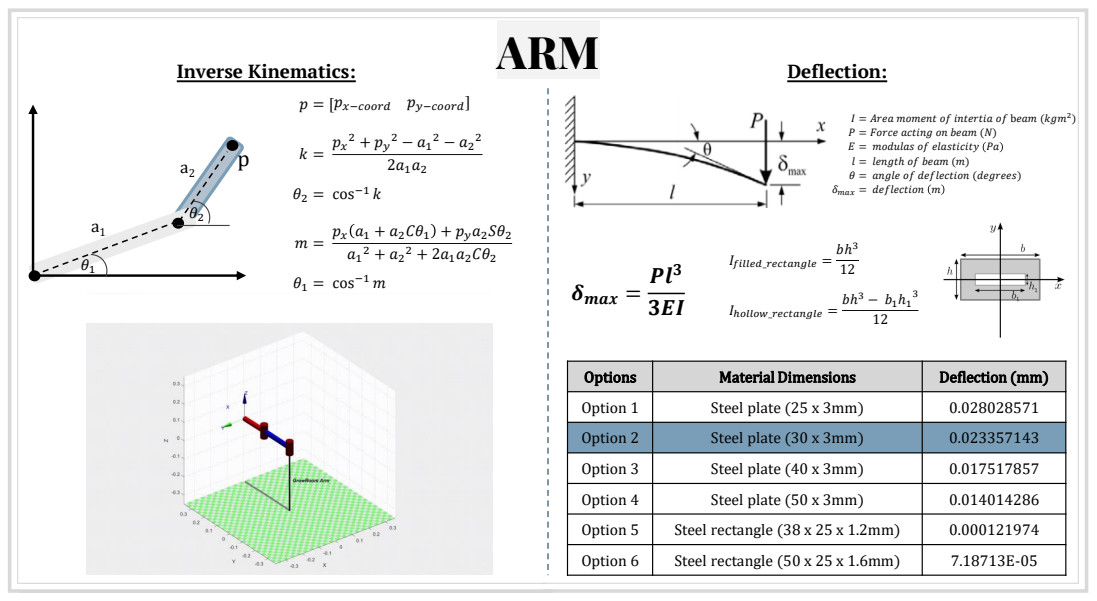
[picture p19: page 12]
p = [px−coord; py−coord]; θ2 = cos⁻¹ k; px a1 + a2Cθ1 + pya2Sθ2 a1; θ1 = cos⁻¹ m; Deflection:; Inverse Kinematics:; ARM; Ifilled_rectangle =; Iℎollow_rectangle =; δmax =

I = Area moment of intertia of beam (kgm²
P = Force acting on beam (N)
E = modulas of elasticity Pa
l = lengtℎ of beam (m)
θ = angle of deflection (degrees)
δmax = deflection m

Options | Material Dimensions | Deflection (mm)

Option 1 | Steel plate (25 x 3mm) | 0.028028571

Option 2 | Steel plate (30 x 3mm) | 0.023357143

Option 3 | Steel plate (40 x 3mm) | 0.017517857

Option 4 | Steel plate (50 x 3mm) | 0.014014286

Option 5 | Steel rectangle (38 x 25 x 1.2mm) | 0.000121974

Option 6 | Steel rectangle (50 x 25 x 1.6mm) | 7.18713E-05

# LINEAR TRANSMISSION ANALYSIS

Linear Transmission System
Type | Cost | Accuracy | Size | Stability | Availability | Weighted Total
Lead Screw | 1.43 | 0.57 | 0.29 | 0.29 | 0.07 | 2.6
Ball Screw | 1.43 | 0.29 | 0.29 | 0.29 | 0.07 | 2.4
Timing Belt | 0.57 | 0.86 | 0.07 | 0.57 | 0.07 | 2.1
Rack and Pinion | 1.43 | 0.29 | 0.14 | 0.57 | 0.36 | 2.8
A | B | C | D | E
Cost | Accuracy | Size | Stability | Availability
A | Cost | AB | A | AD | A
B | Accuracy | | B | BD | B
C | Size | | | D | CE
D | Stability | | | | D
E Availability

Weightings
A 0.29
B 0.29
C 0.07
D 0.29
E 0.07

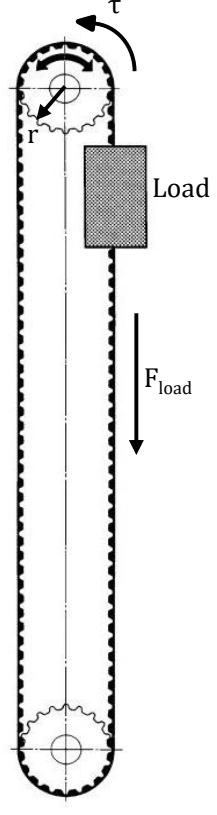
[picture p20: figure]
Load; Fload

# CURRENT PROGRESS: ANALYSIS

τ

# CURRENT PROGRESS: ANALYSIS

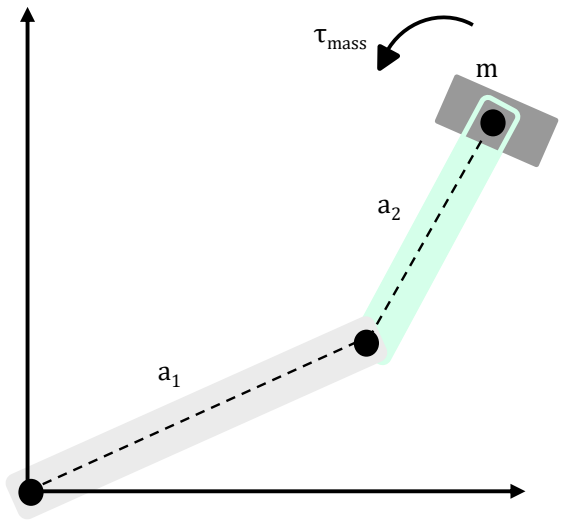
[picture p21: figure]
τmass

# CURRENT PROGRESS: ANALYSIS

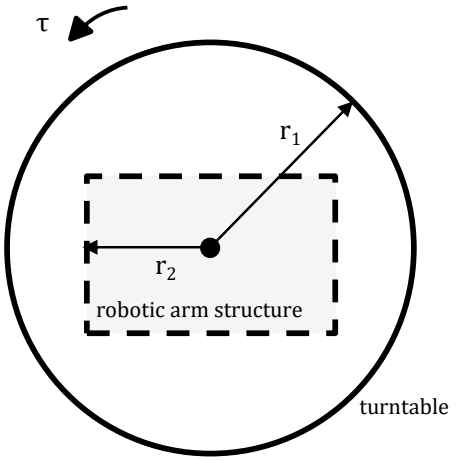
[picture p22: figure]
robotic arm structure; turntable

# MOTOR SELECTION ANALYSIS

Linear Actuation
Motor | Precision/Control | Torque Capability | Size/Weight | Cost | Total
AC | 5 | Yes | Implementation Dependent | 4 | 9
DC Brushed | 5 | Yes | | 3 | 8
DC Brushed with Encoder | 1 | Yes | | 4 | 5
DC Brushless | 5 | Yes | | 2 | 7
DC Brushless with Encoder | 1 | Yes | | 4 | 5
Servo Motors | 2 | Maybe | | 1 | 3
Stepper Motors | 1 | Yes | | 2 | 3
Motor | Torque (Ncm) | Torque (Nm) | Cost (AUD) | Weight (kg) | Dimensions (mm)
Nema 17 Unipolar 1.8deg 15.8Ncm (22.4oz.in) 0.31A 12V 42x42x33mm 6 Wires | 15.8 | 0.158 | 13.77 | 0.22 | 42 x 42 x 33
Nema 17 Bipolar 1.8deg 16Ncm (22.6oz.in) 1A 3.7V 42x42x20mm 4 Wires | 16 | 0.16 | 12.08 | 0.14 | 42 x 42 x 20
Nema 17 Unipolar 1.8deg 16Ncm (22.7oz.in) 0.95A 4V 42x42x33mm 6 Wires | 16 | 0.16 | 13.77 | 0.22 | 42 x 42 x 33
Dual Shaft Nema 14 1.8deg 18Ncm (25.56oz.in) 0.8A 5.4V 35.2x35.2x34mm 4 Wires | 18 | 0.18 | 14.96 | 0.17 | 35.2 x 35.2 x 34
Nema 14 Bipolar 1.8deg 18Ncm (25.5oz.in) 0.8A 5.4V 35x35x34mm 4 Wires | 18 | 0.18 | 12.56 | 0.19 | 35 x 35 x 34

# MOTOR SELECTION ANALYSIS

Linear Actuation
Motor | Precision/Control | Torque Capability | Size/Weight | Cost | Total
AC | 5 | Yes | Implementation Dependent | 4 | 9
DC Brushed | 5 | Yes | | 3 | 8
DC Brushed with Encoder | 1 | Yes | | 4 | 5
DC Brushless | 5 | Yes | | 2 | 7
DC Brushless with Encoder | 1 | Yes | | 4 | 5
Servo Motors | 2 | Requirement Dependent | | 1 | 3
Stepper Motors | 1 | Yes | | 2 | 3
Motor | Torque (Ncm) | Torque (Nm) | Cost (AUD) | Weight (kg) | Dimensions (mm)
Nema 17 Unipolar 1.8deg 15.8Ncm (22.4oz.in) 0.31A 12V 42x42x33mm 6 Wires | 15.8 | 0.158 | 13.77 | 0.22 | 42 x 42 x 33
Nema 17 Bipolar 1.8deg 16Ncm (22.6oz.in) 1A 3.7V 42x42x20mm 4 Wires | 16 | 0.16 | 12.08 | 0.14 | 42 x 42 x 20
Nema 17 Unipolar 1.8deg 16Ncm (22.7oz.in) 0.95A 4V 42x42x33mm 6 Wires | 16 | 0.16 | 13.77 | 0.22 | 42 x 42 x 33
Dual Shaft Nema 14 1.8deg 18Ncm (25.56oz.in) 0.8A 5.4V 35.2x35.2x34mm 4 Wires | 18 | 0.18 | 14.96 | 0.17 | 35.2 x 35.2 x 34
Nema 14 Bipolar 1.8deg 18Ncm (25.5oz.in) 0.8A 5.4V 35x35x34mm 4 Wires | 18 | 0.18 | 12.56 | 0.19 | 35 x 35 x 34

# CAD

# FUTURE PLAN

## What is left to do?

20

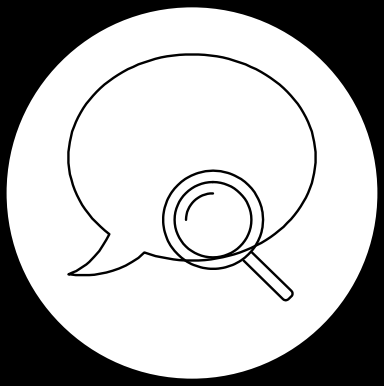
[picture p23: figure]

# Questions?

## Thank-you for listening!

## Instructions for use

EDIT IN GOOGLE SLIDES
Click on the button under the presentation preview that says "Use as Google Slides Theme".
You will get a copy of this document on your Google Drive and will be able to edit, add or delete slides.
You have to be signed in to your Google account.

EDIT IN POWERPOINT®
Click on the button under the presentation preview that says "Download as PowerPoint template". You will get a .pptx file that you can edit in PowerPoint.
Remember to download and install the fonts used in this presentation (you’ll find the links to the font files needed in the Presentation design slide)

More info on how to use this template at www.slidescarnival.com/help-use-presentation-template (http://www.slidescarnival.com/help-use-presentation-template)
This template is free to use under Creative Commons Attribution license. (http://www.slidescarnival.com/copyright-and-legal-information) You can keep the Credits slide or mention SlidesCarnival and other resources used in a slide footer.

22

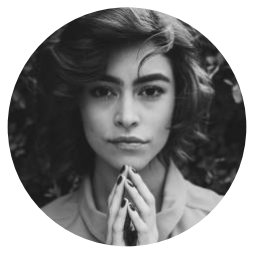
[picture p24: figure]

# hello!

# I am Jayden Smith

I am here because I love to give presentations.

## You can find me at @username

23

1.

# Transition headline

## Let’s start with the first set of slides

24

“

## Quotations are commonly printed as a means of inspiration and to invoke philosophical thoughts

from the reader.

25

## This is a slide title

## ▣ Here you have a list of items ▣ And some text ▣ But remember not to overload your slides with content

## Your audience will listen to you or read the content, but

won’t do both.

26

# White

## Is the color of milk and fresh snow, the color produced by the combination of all the colors of

the visible spectrum.

## You can also split your content

# Black

## Is the color of coal, ebony, and of outer space. It is the darkest color, the result of the absence of or complete absorption of

light.

27

## In two or three columns

## Yellow

Is the color of gold,
butter and ripe lemons.

## In the spectrum of visible light, yellow is found between green and

orange.

## Blue

## Is the colour of the clear sky and the deep sea. It is located between violet and green on the optical

spectrum.

## Red

## Is the color of blood, and because of this it has historically been

associated with sacrifice, danger and courage.

28

## A picture is worth a thousand words

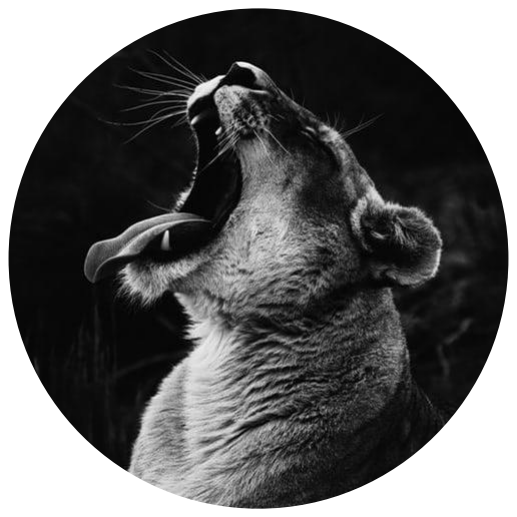
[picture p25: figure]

A complex idea can be conveyed with just a single still image, namely making it possible to absorb large amounts of data quickly.

29

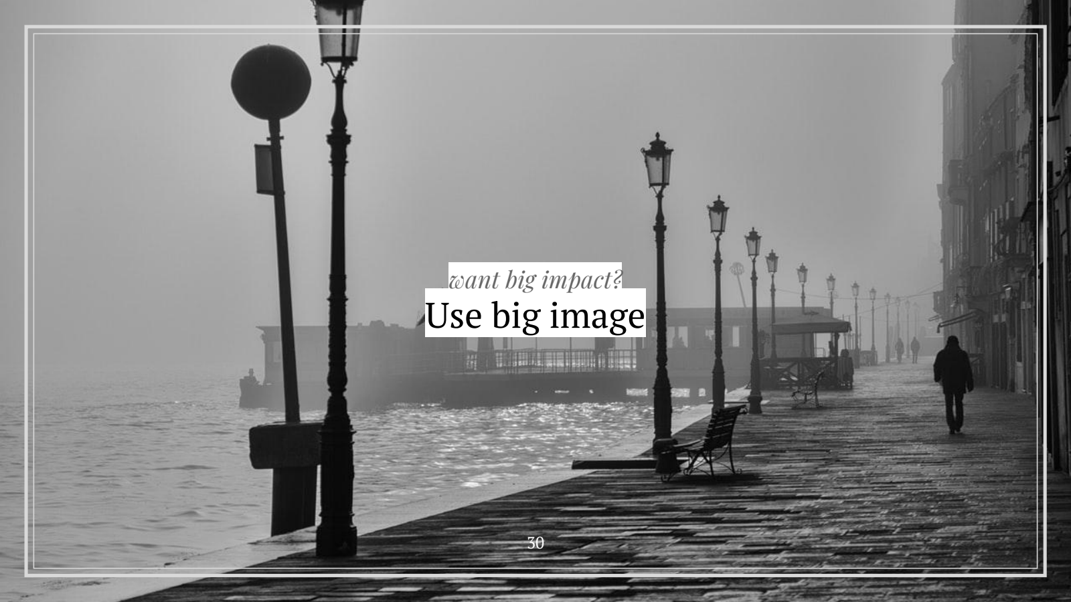
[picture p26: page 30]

## want big impact?

# Use big image

30

## Use charts to explain your ideas

White | Gray | Black

31

## And tables to compare data

A | B | C
Yellow | 10 | 20 | 7
Blue | 30 | 15 | 10
Orange | 5 | 24 | 16

32

## Maps

our office

89,526,124

## Whoa! That’s a big number, aren’t you proud?

34

89,526,124$

## That’s a lot of money

100%

## Total success!

# 185,244 users

## And a lot of users

35

## Our process is easy

first | second | last

36

## Let’s review some concepts

## Yellow

Is the color of gold, butter and ripe lemons. In the spectrum of visible light, yellow is found between green and orange.

## Blue

Is the colour of the clear sky and the deep sea. It is located between violet and green on the optical spectrum.

## Red

Is the color of blood, and because of this it has historically been associated with sacrifice, danger and courage.

## Yellow

Is the color of gold, butter and ripe lemons. In the spectrum of visible light, yellow is found between green and orange.

## Blue

Is the colour of the clear sky and the deep sea. It is located between violet and green on the optical spectrum.

## Red

Is the color of blood, and because of this it has historically been associated with sacrifice, danger and courage.

37


You can copy&paste graphs from 38 Google Sheets (http://www.google.com/sheets/about/)

Place your screenshot here

## Mobile project

## Show and explain your web, app or software projects using these

gadget templates.

39

Place your screenshot here

## Tablet project

Show and explain your web,

## app or software projects using these gadget

templates.

40

## Desktop project

Place your screenshot here

## Show and explain your web, app or software projects using these

gadget templates.

41

# thanks!

# Any questions?

## You can find me at @username user@mail.me

42

## Credits

# Special thanks to all the people who made and released these awesome resources for free: ▣ Presentation template by SlidesCarnival (http://www.slidescarnival.com/) ▣ Photographs by Unsplash (http://unsplash.com/)

43

## Presentation design

## This presentations uses the following typographies: ▣ Titles: Playfair Display ▣ Body copy: PT Serif You can download the fonts on this page: https://www.fontsquirrel.com/fonts/playfair-display https://www.fontsquirrel.com/fonts/pt-serif

You don’t need to keep this slide in your presentation. It’s only here to serve you as a design guide if you need to create new slides or download the fonts to edit the presentation in PowerPoint®

44


SlidesCarnival icons are editable shapes.
This means that you can:
● Resize them without losing quality.
● Change line color, width and style.
Isn’t that nice? :)
Examples:

Now you can use any emoji as an icon!
And of course it resizes without losing quality and you can change the color.

How? Follow Google instructions https://twitter.com/googledocs/status/730087240156643328
✋👆👉👍👤👦👧👨👩👪💃🏃
💑❤😂😉😋😒😭👶😸🐟🍒
🍔💣📌📖🔨🎃🎈🎨🏈🏰🌏
🔌🔑and many more...

😉

46


## Free templates for all your presentation needs

Ready to use,
professional and
customizable

100% free for personal
or commercial use

Blow your audience
away with attractive
visuals

For PowerPoint and
Google Slides

47

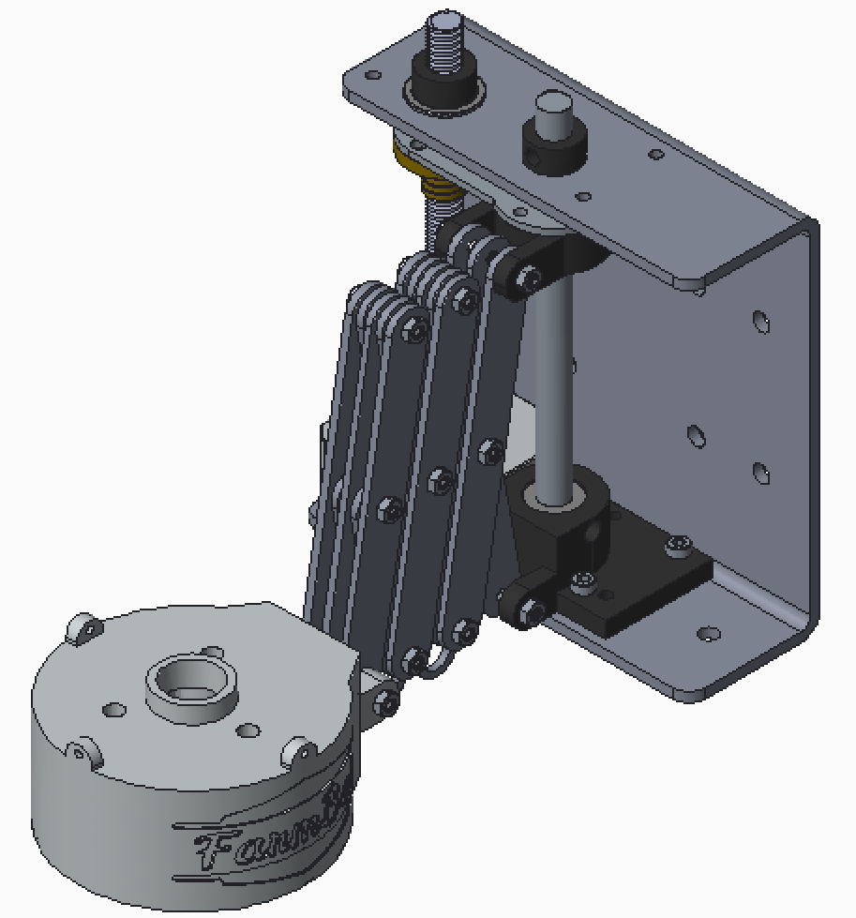
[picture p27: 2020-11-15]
CAD Model/Mechanical Drawings/Renders/arm.PNG

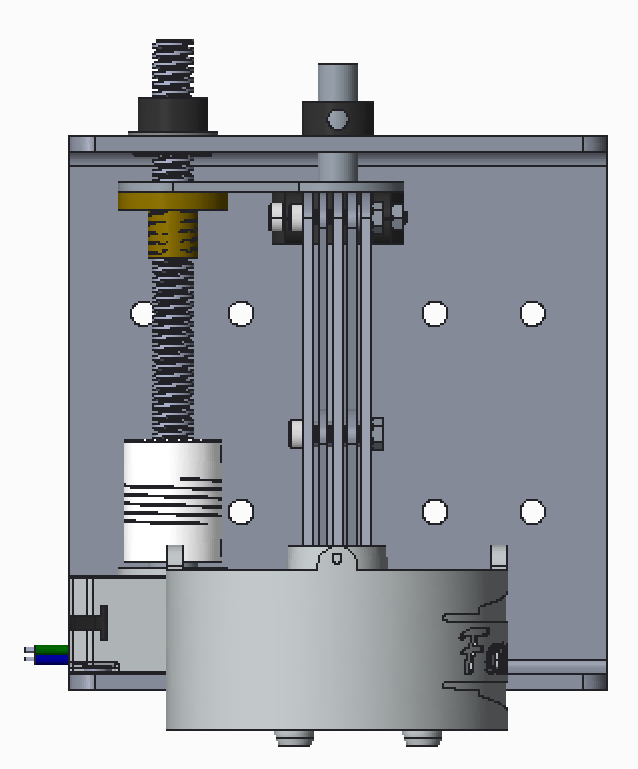
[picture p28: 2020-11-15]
CAD Model/Mechanical Drawings/Renders/frontArm.PNG

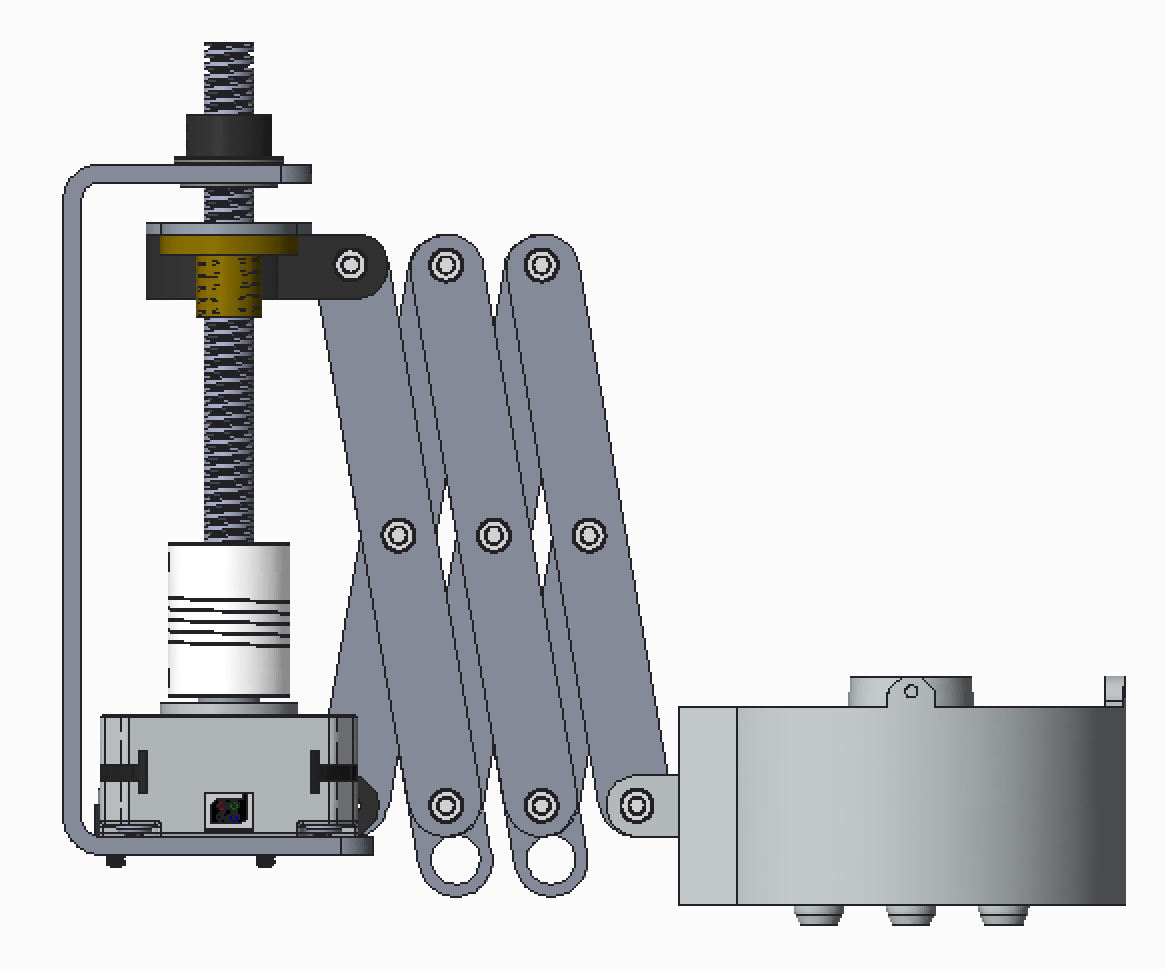
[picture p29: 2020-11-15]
CAD Model/Mechanical Drawings/Renders/sideArm.PNG

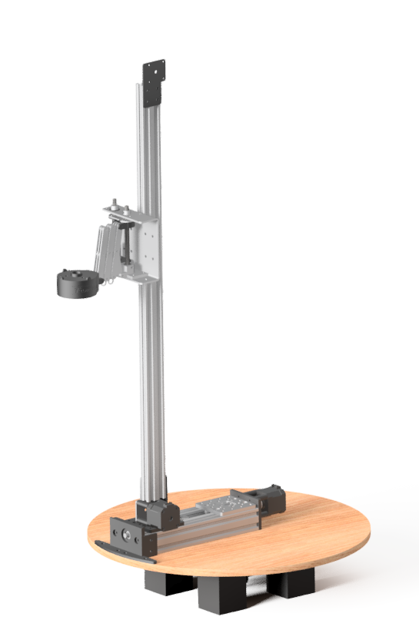
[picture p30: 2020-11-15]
CAD Model/Mechanical Drawings/Renders/robot.png

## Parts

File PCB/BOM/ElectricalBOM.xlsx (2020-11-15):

The Monarch Receiver PCB
Part Number/Name | Description/Value | Designator | LibRef | Quantity | Unit Price | Total Price | Source | URL/Bin Number
theMonarchReceiver PCB |  |  |  | 5 | 1.954 | 9.77 | JLCPCP
Capacitor | 10uF | C4 | Cap | 1 | 1.59 | 1.59 | ETSG | 07-68-03
Capacitor | 100uF | C1,C2,C3 | Cap | 3 | 0.48 | 1.44 | ETSG | 07-58-03
Resistor | 1K | R4 | Res1 | 1 | 0.03 | 0.03 | ETSG | 02-25-02
Resistor | 10K | R1, R2, R3, R5, R6, R7 | Res1 | 6 | 0.03 | 0.18 | ETSG | 02-33-02
A4988 | Stepper Driver | IC1, IC2, IC3 | a4988 | 3 | 6.5 | 19.5 | Makerstore |  | https://www.makerstore.com.au/product/elec-a4988/
FC681478 | Power Jack | J1 | FC681478 | 1 | 2.31 | 2.31 | Element14 |  | https://au.element14.com/cliff-electronic-components/fc681478/connector-power-entry-rcpt-2a/dp/2450496
8 Pin Header | 8 Pin Header | IC1, IC2, IC3, J2 | WRL-00691 | 7 | 1.72 | 12.04 | ETSG | 03-38-03
S2B-XH-A | 2 Pin Header (right-angle) | P1, P5, P7, P11, P13, P15, P17, P18 | S2B-XH-A(LF) | 8 | 0.27 | 2.16 | ETSG | 08-52-03
S4B-XH-A | 4 Pin Header (right-angle) | P2, P8, P12 | 4B-XH-A(LF)(SN) | 3 | 0.69 | 2.07 | ETSG | 08-53-01
826936-3 | 3 Pin Header | P3, P19 | 826936-3 | 2 | 0.86 | 1.72 | ETSG | 08-34-01 | P3 used as power tester - header not required here
B2B-PH-K-S | 2 Pin Header | P4, P6, P10, P14 | B2B-PH-K-S(LF)(SN) | 4 | 0.151 | 0.604 | Element14 |  | https://au.element14.com/jst-japan-solderless-terminals/b2b-ph-k-s-lf-sn/header-top-entry-2way-2mm/dp/9491856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
HDR1X5 | 5 Pin Header | P16 | HDR1X5 | 1 | 0.63 | 0.63 | ETSG | 03-38-01
LED | LED (green) | P9 | LED | 1 | 0.08 | 0.08 | ETSG | 04-49-01
DB1C-A1LB | Micro Switch | - | - | 6 | 2.81 | 16.86 | ETSG | 04-91-03
nRF24L01+ | Transceiver | J2 | WRL-00691 | 1 | 20.95 | 20.95 | Sparkfun |  | https://www.sparkfun.com/products/691
K143 Crimps | JST Crimps |  |  | 40 | 0.02 | 0.8 | ETSG | 08-50-03 | 119.134
JST PHR-2 | JST Terminal Housing (2 Pin) |  |  | 10 | 0.07 | 0.7 | ETSG | 08-49-01
JST PHR-4 | JST Terminal Housing (4 Pin) |  |  | 3 | 0.09 | 0.27 | ETSG | 08-49-02
Nylon Screw | M3.0 x 6mm Nylon Bolt |  |  | 2 | 0.13 | 0.26 | ETSG | 10-34-01
Nylon Hex Nut | M3.0 Nylon Nut |  |  | 2 | 0.11 | 0.22 | ETSG | 10-38-01
SMP12V-3A-21P | Power Pack |  |  | 1 | 24.95 | 24.95 | Wagner |  | https://www.wagneronline.com.au/12-volt-3a-switch-mode/power-supplies/power-lighting/smp12v-3a-21p-69272/976406/pd/
WemosESP8266
WemosESP8266 PCB |  |  |  | 5 | 1.396 | 6.98 | JLCPCP
Capacitor | 10uF | C2 | Cap | 1 | 1.59 | 1.59 | ETSG | 07-68-03 | 99.261
Capacitor | 100uF | C1 | Cap | 1 | 0.48 | 0.48 | ETSG | 07-58-03
Resistor | 1K | R2, R3 | Res1 | 1 | 0.03 | 0.03 | ETSG | 02-25-02
Resistor | 10K | R1 | Res1 | 2 | 0.03 | 0.06 | ETSG | 02-33-02
A4988 | Stepper Driver | IC1 | a4988 | 1 | 6.5 | 6.5 | Makerstore |  | https://www.makerstore.com.au/product/elec-a4988/
FC681478 | Power Jack | J1 | FC681478 | 1 | 2.31 | 2.31 | Element14 |  | https://au.element14.com/cliff-electronic-components/fc681478/connector-power-entry-rcpt-2a/dp/2450496
8 Pin Header | 8 Pin Header | IC1, J2 | WRL-00691 | 3 | 1.72 | 5.16 | ETSG | 03-38-03
S7036-ND | 3 Pin Header | J3, J4 | 826936-3 | 2 | 0.86 | 1.72 | ETSG | 08-34-01 | J3 used as power tester - not required here
S4B-XH-A | 4 Pin Header (right-angle) | P1 | 4B-XH-A(LF)(SN) | 3 | 0.69 | 2.07 | ETSG | 08-53-01
HDR1X5 | 5 Pin Header | P2 | HDR1X5 | 1 | 0.63 | 0.63 | ETSG | 03-38-01
S2B-XH-A | 2 Pin Header (right-angle) | P3, P4, P6, P7 | S2B-XH-A(LF)(SN) | 4 | 0.27 | 1.08 | ETSG | 08-52-03
B2B-PH-K-S | 2 Pin Header | P5 | B2B-PH-K-S(LF)(SN) | 1 | 0.151 | 0.151 | Element14 |  | https://au.element14.com/jst-japan-solderless-terminals/b2b-ph-k-s-lf-sn/header-top-entry-2way-2mm/dp/9491856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
LED | LED (green) | P9 | LED | 1 | 0.08 | 0.08 | ETSG | 04-49-01
DB1C-A1LB | Micro Switch | - | - | 1 | 2.81 | 2.81 | ETSG | 04-91-03
nRF24L01+ | Transceiver | J2 | WRL-00691 | 1 | 20.95 | 20.95 | Sparkfun |  | https://www.sparkfun.com/products/691
K143 Crimps | JST Crimps |  |  | 40 | 0.02 | 0.8 | ETSG | 08-50-03
JST PHR-2 | JST Terminal Housing (2 Pin) |  |  | 5 | 0.07 | 0.35 | ETSG | 08-49-01
JST PHR-4 | JST Terminal Housing (4 Pin) |  |  | 1 | 0.09 | 0.09 | ETSG | 08-49-02
Nylon Screw | M3.0 x 6mm Nylon Bolt |  |  | 2 | 0.13 | 0.26 | ETSG | 10-34-01
Nylon Hex Nut | M3.0 Nylon Nut |  |  | 2 | 0.11 | 0.22 | ETSG | 10-38-01
SMP12V-3A-21P | Power Pack |  |  | 1 | 24.95 | 24.95 | Wagner |  | https://www.wagneronline.com.au/12-volt-3a-switch-mode/power-supplies/power-lighting/smp12v-3a-21p-69272/976406/pd/
 |  |  |  |  |  | 19.99
 |  |  |  |  |  | 218.395

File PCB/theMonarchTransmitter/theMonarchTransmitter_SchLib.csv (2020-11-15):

LIBRARYREFERENCE | CATEGORY | COMMENT | COMPONENTLINK1DESCRIPTION | COMPONENTLINK1URL | DESCRIPTION | FREQUENCY | MANUFACTURER | MANUFACTURER PART NUMBER | PRICING 1 | ROHS | STOCK 1 | SUPPLIER 1 | SUPPLIER PART NUMBER 1 | SHEETPART | DESIGNATOR | DESCRIPTION
Component_1 |  | * |  |  |  |  |  |  |  |  |  |  |  | * | *
WRL-00691 | RF Semiconductors and Devices | nRF24L01+ | https://github.com/sparkfun/Transceiver_Breakout-nRF24L01/tree/V_1.3?src-supplier=Digi-Key | https://github.com/sparkfun/Transceiver_Breakout-nRF24L01/tree/V_1.3?src-supplier=Digi-Key | SPARKFUN TRANSCEIVER BREAKOUT - | 2.4GHz | SparkFun | WRL-00691 | 1=20.95000 (USD) | No | 59 | Digi-Key | 1568-1295-ND | * | J? | SPARKFUN TRANSCEIVER BREAKOUT -

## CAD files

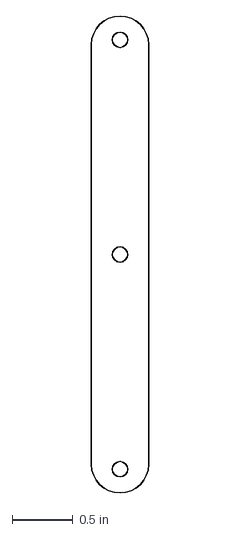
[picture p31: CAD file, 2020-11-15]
CAD Model/FINAL/arm/Scissor/Scissors/full_length_scissor.dxf
0.472 x 3.94 in

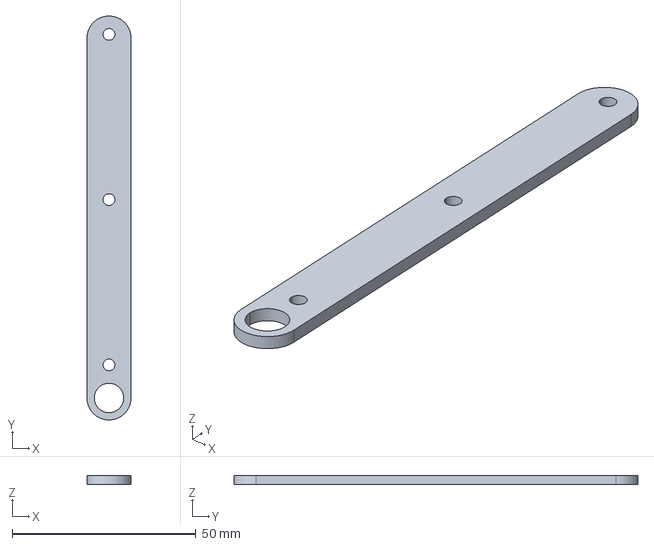
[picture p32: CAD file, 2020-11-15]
CAD Model/FINAL/arm/Scissor/Scissors/scissor_full_cable.stp
12.0 x 110.0 x 2.50 mm

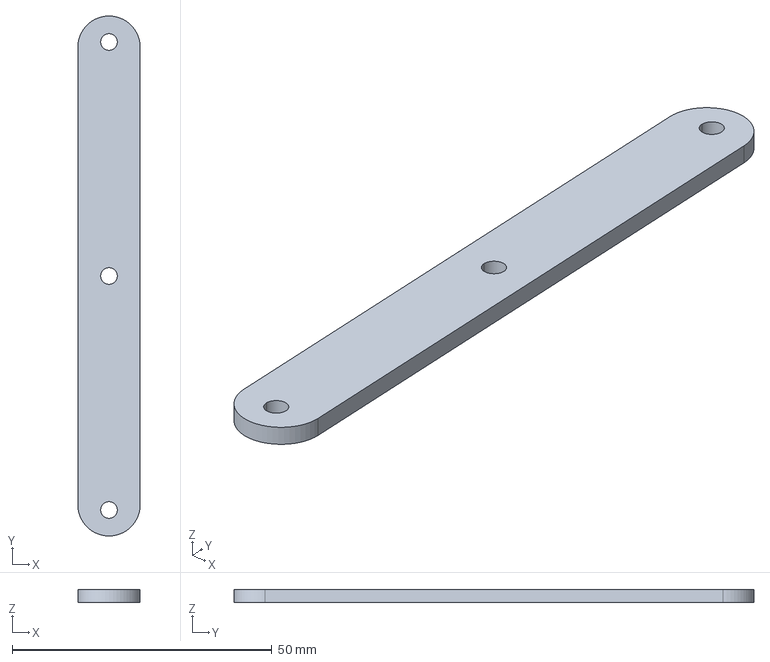
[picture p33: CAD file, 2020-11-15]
CAD Model/FINAL/arm/Scissor/Scissors/scissor_full_length.stp
12.0 x 100.0 x 2.50 mm

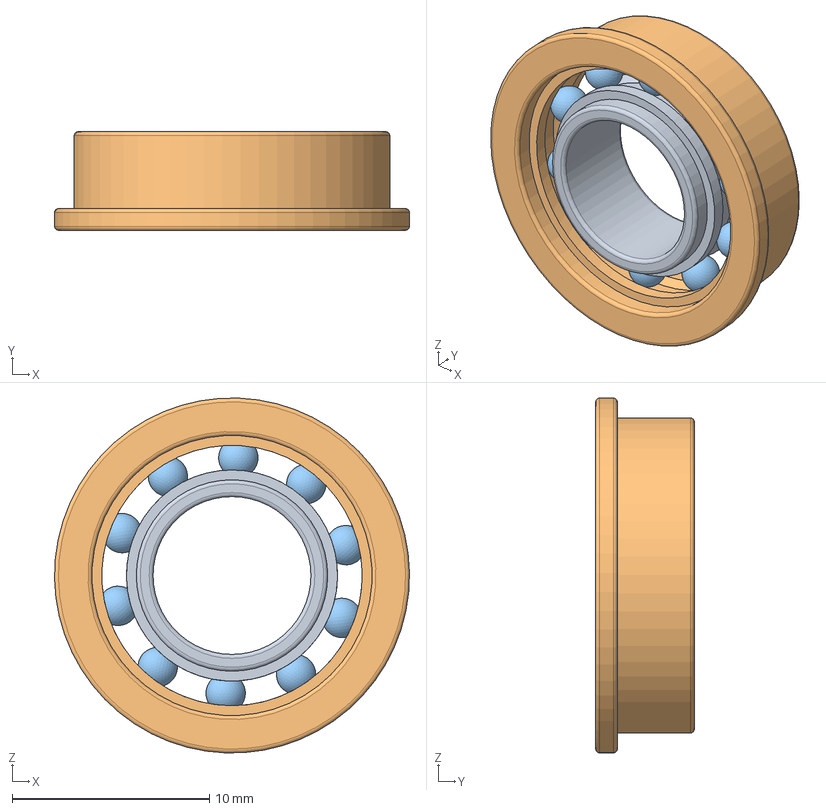
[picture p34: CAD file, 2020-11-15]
CAD Model/FINAL/arm/Scissor/F688ZZ_assembly.stp
18.0 x 5.00 x 18.0 mm
F688ZZ_shaft
F688ZZ_Housing
F688ZZ_Ball x 10

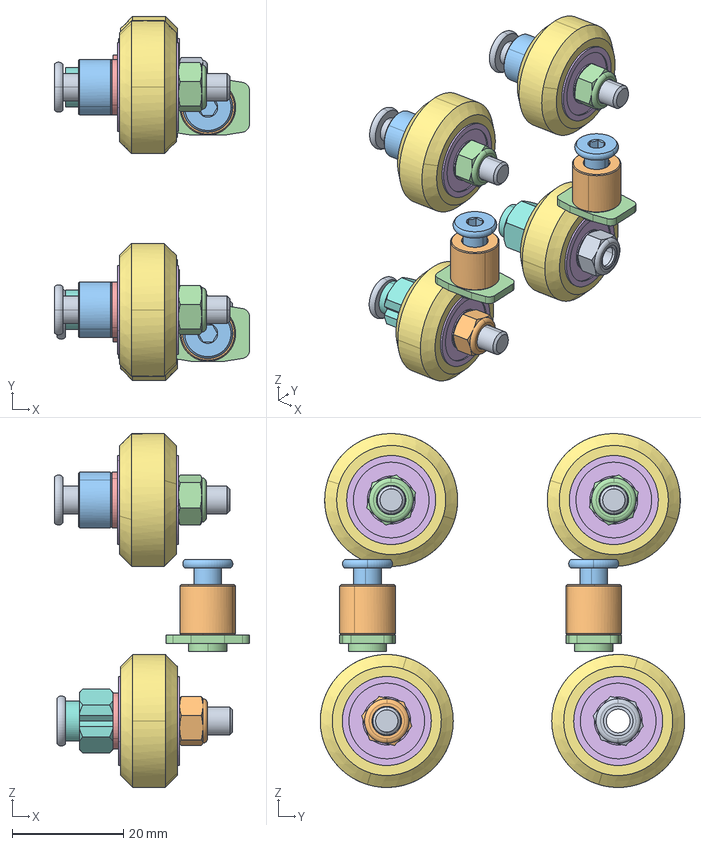
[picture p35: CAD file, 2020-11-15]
CAD Model/FINAL/arm/Scissor/wheel_assembly_asm.stp
35.1 x 65.5 x 63.6 mm
LOW_PROFILE_SCREW_M5_V1 x 3

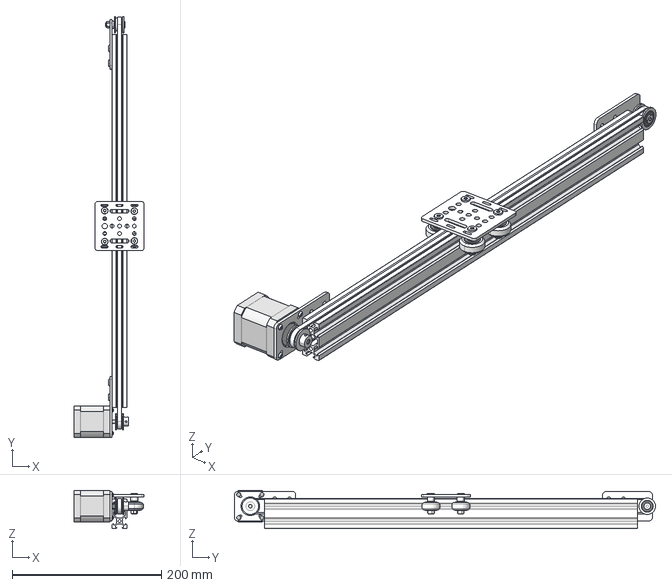
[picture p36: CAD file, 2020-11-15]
CAD Model/FINAL/additionalComponents/Nema 17 V Slot Belt Driven Actuator 500mm.stp
93.8 x 564.2 x 51.2 mm

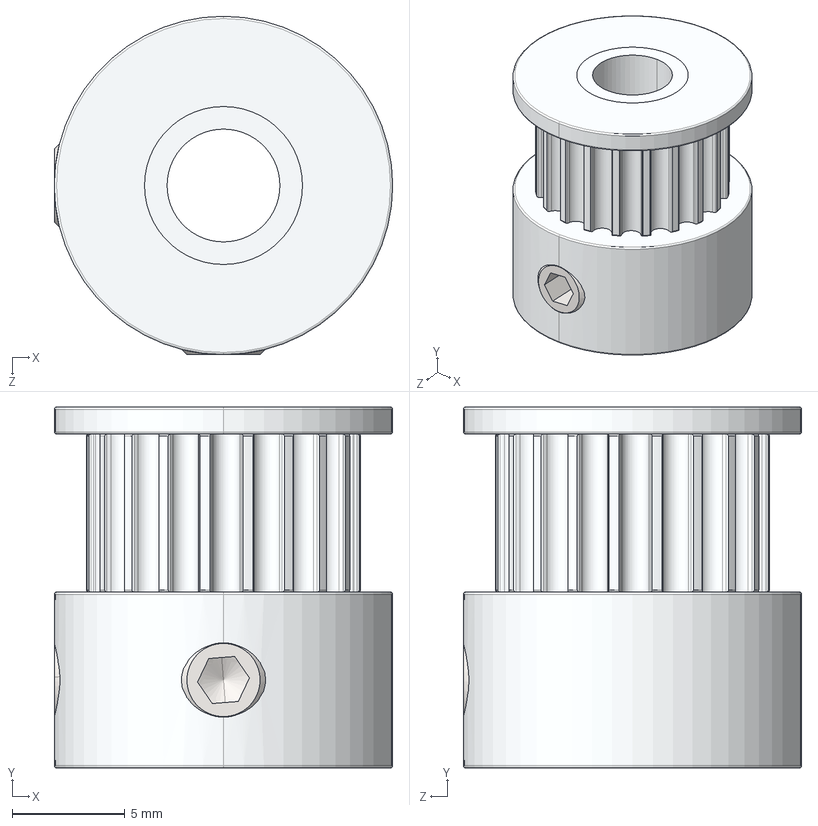
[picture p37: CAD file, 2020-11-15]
CAD Model/FINAL/arm/SCARA/Gates_2GT_20T_Toothed_Pulley.STEP
15.0 x 16.0 x 15.0 mm
Gates_2GT_20T_Toothed_Pulley_01
Gates_2GT_20T_Toothed_Pulley_02
Gates_2GT_20T_Toothed_Pulley_03
screw_iso_4026-m4x5 x 2

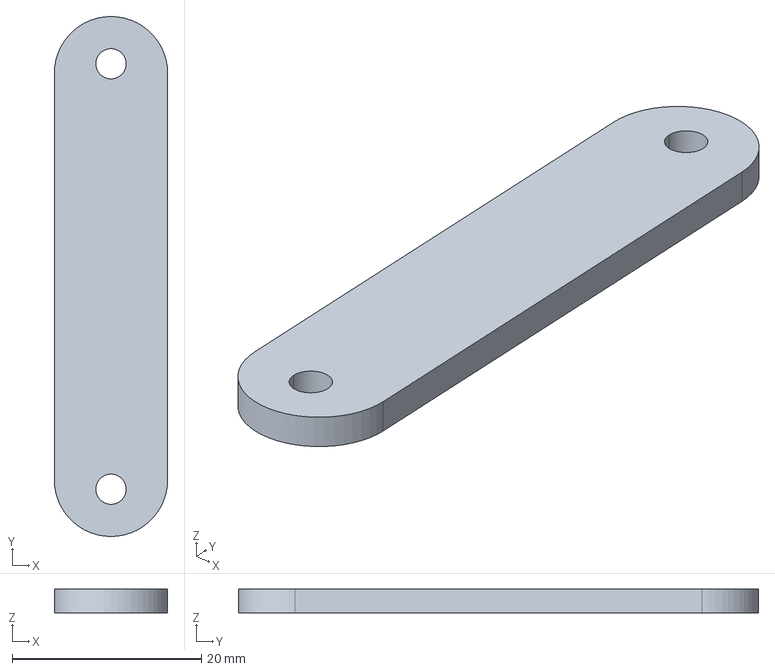
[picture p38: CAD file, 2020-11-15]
CAD Model/FINAL/arm/Scissor/Scissors/half_scissor.stp
12.0 x 55.0 x 2.50 mm

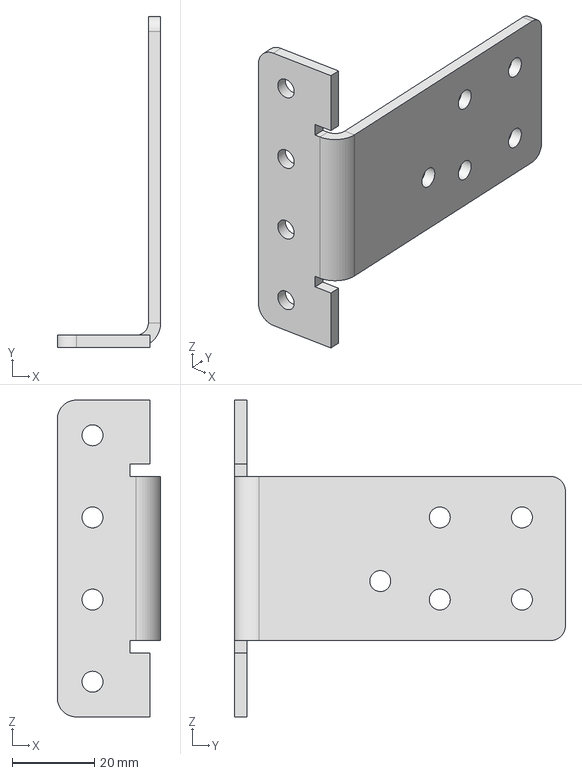
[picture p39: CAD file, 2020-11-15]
CAD Model/FINAL/brackets/Assembly/long_bracket_folded.stp
25.2 x 80.6 x 77.2 mm

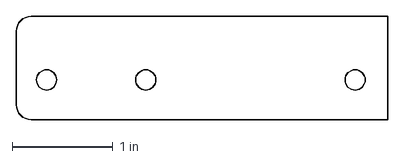
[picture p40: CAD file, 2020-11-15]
CAD Model/FINAL/brackets/Manufacture/Waterjet/short_bracket_flat_pattern.dxf
3.68 x 1.02 in

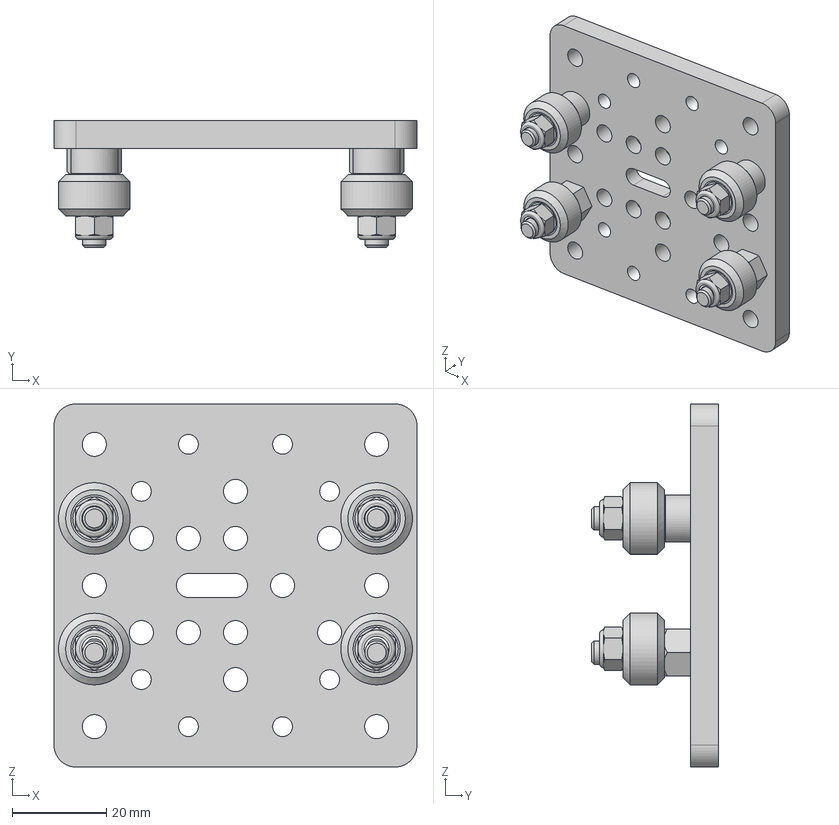
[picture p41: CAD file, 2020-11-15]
CAD Model/FINAL/c-beam/C-Beam Gantry Kit.step
77.2 x 27.0 x 77.2 mm
Low Profile Screw M5 v1 x 4
Nylon Insert Lock Nut M5 x 4
Precision Shim 8 x 5 x 1 x 4
Eccentric Spacer 6mm v1 x 2
Aluminum Spacer 6mm x 2
Ball Bearing 5 x 10 x 4.2 x 8
C-Beam Gantry Plate
Xtreme Mini V Wheel x 4

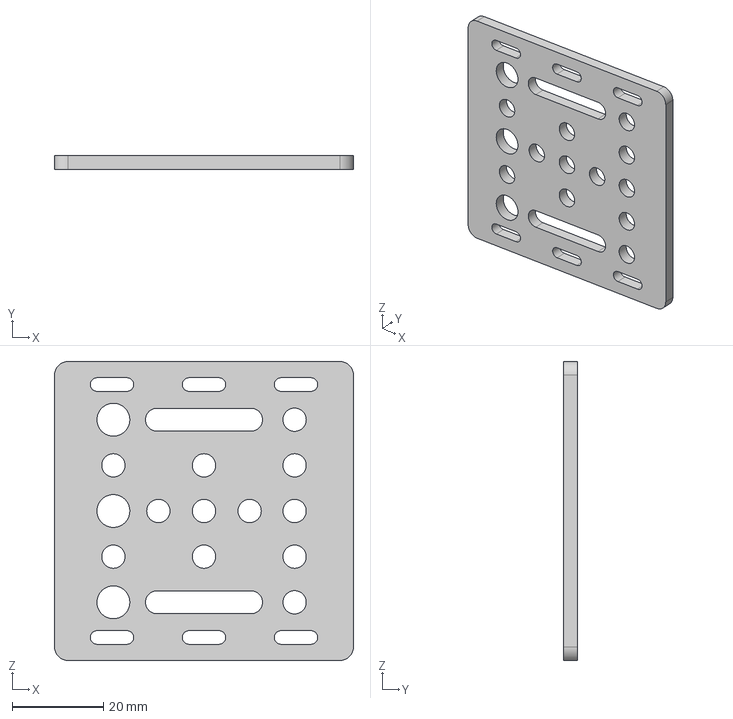
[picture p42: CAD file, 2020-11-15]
CAD Model/FINAL/centre_beam/V-Slot Gantry Plate 20mm.step
65.5 x 3.00 x 65.5 mm

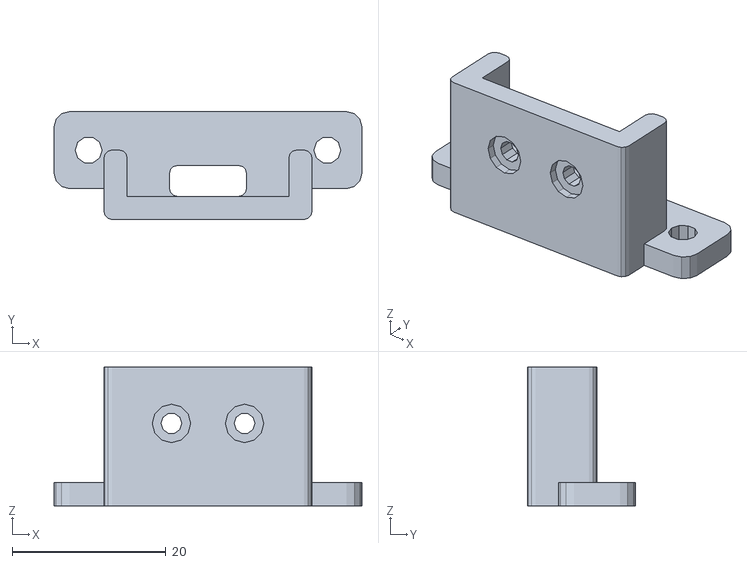
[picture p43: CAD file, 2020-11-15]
CAD Model/FINAL/switches/limit_switch_holder.stl
40.0 x 14.0 x 18.0

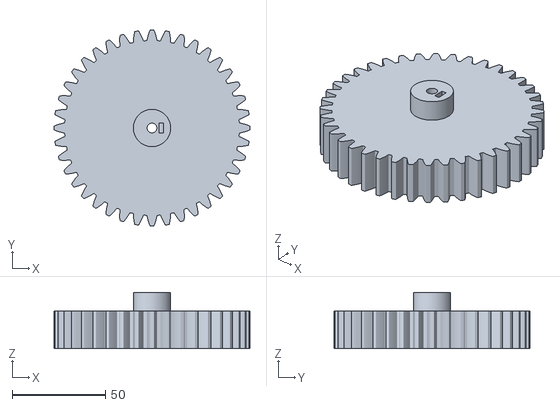
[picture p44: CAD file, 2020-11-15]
CAD Model/FINAL/turntable/Gears/4to1Gear2.stl
105.0 x 105.0 x 30.0

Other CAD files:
CAD Model/FINAL/brackets/Manufacture/Drawings/folded_arm_bracket.dwg
CAD Model/FINAL/brackets/Manufacture/StepCreoFiles/long_bracket_folded.stp
CAD Model/FINAL/turntable/nema23.step
PCB/theMonarchTransmitter/theMonarchTransmitter.step
CAD Model/FINAL/arm/SCARA/UTM.step
CAD Model/FINAL/arm/Scissor/100mm_v_slot_plate.stp
CAD Model/FINAL/arm/Scissor/3mm_spacer.stp
CAD Model/FINAL/arm/Scissor/F688ZZ_assembly.SLDASM
CAD Model/FINAL/arm/Scissor/LeadScrew 8mm x 2mmPitch.STEP
CAD Model/FINAL/arm/Scissor/LeadScrew Nut 8mm x 2mmPitch.STEP
CAD Model/FINAL/arm/Scissor/Lock Collar 8mm.step
CAD Model/FINAL/arm/Scissor/M3 Nut.STEP
CAD Model/FINAL/arm/Scissor/M3 x 0.5mm Thread 10mm LONG SOCKET HEAD CAP SCREW.STEP
CAD Model/FINAL/arm/Scissor/Nylon Insert Lock Nut M5.step
CAD Model/FINAL/arm/Scissor/Scissors/100mm_v_slot_plate.dxf
CAD Model/FINAL/arm/Scissor/Scissors/cable_scissor.dxf
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

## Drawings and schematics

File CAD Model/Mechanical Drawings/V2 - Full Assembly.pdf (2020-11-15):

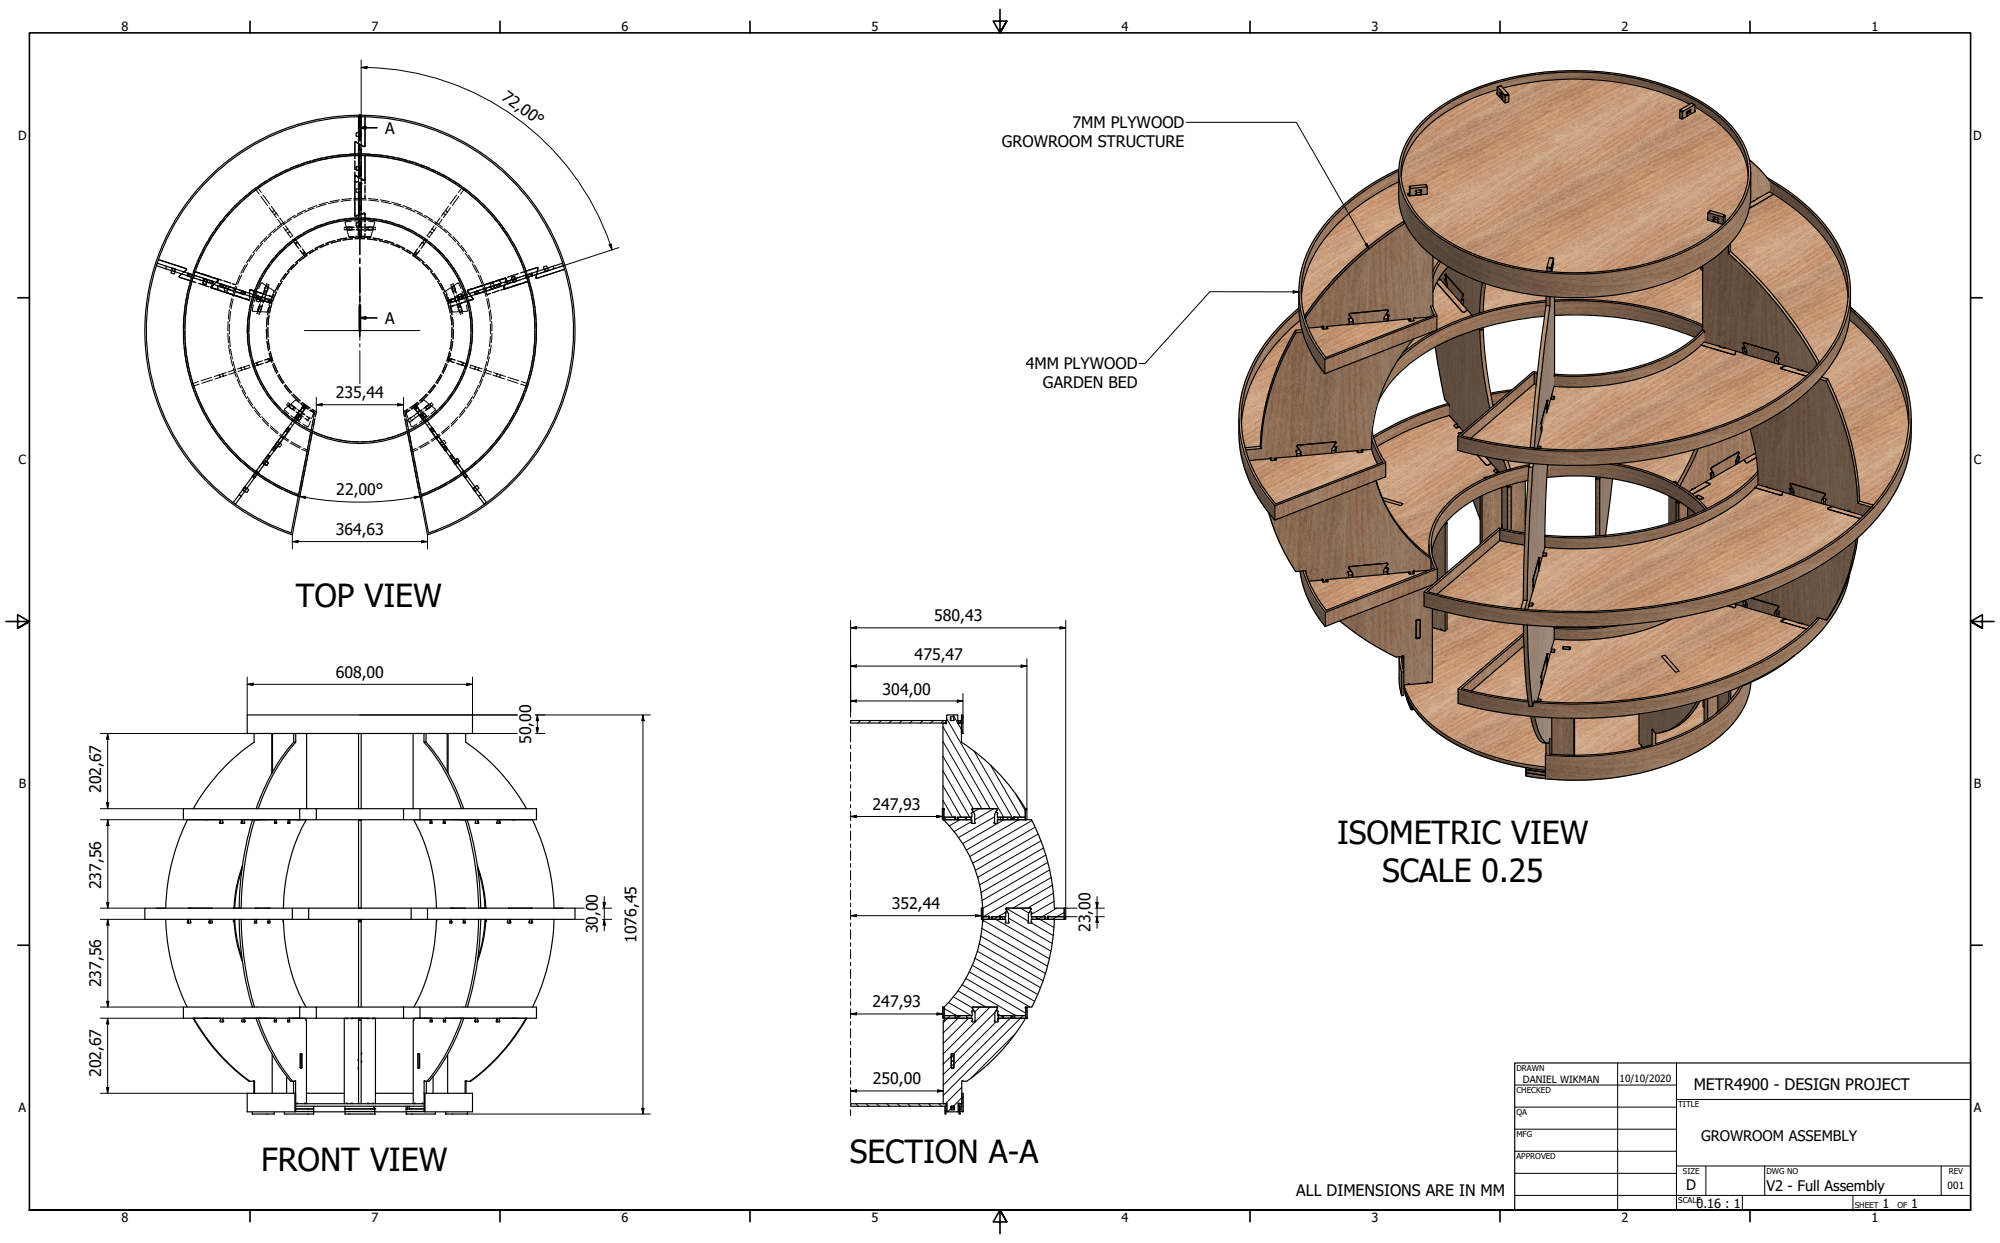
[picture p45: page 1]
FRONT VIEW; ISOMETRIC VIEW SCALE 0.25; TOP VIEW; SECTION A-A; SHEET 1 OF 1; DANIEL WIKMAN; DWG NO V2 - Full Assembly; GROWROOM ASSEMBLY; METR4900 - DESIGN PROJECT; 4MM PLYWOOD GARDEN BED; 7MM PLYWOOD GROWROOM STRUCTURE

ALL DIMENSIONS ARE IN MM

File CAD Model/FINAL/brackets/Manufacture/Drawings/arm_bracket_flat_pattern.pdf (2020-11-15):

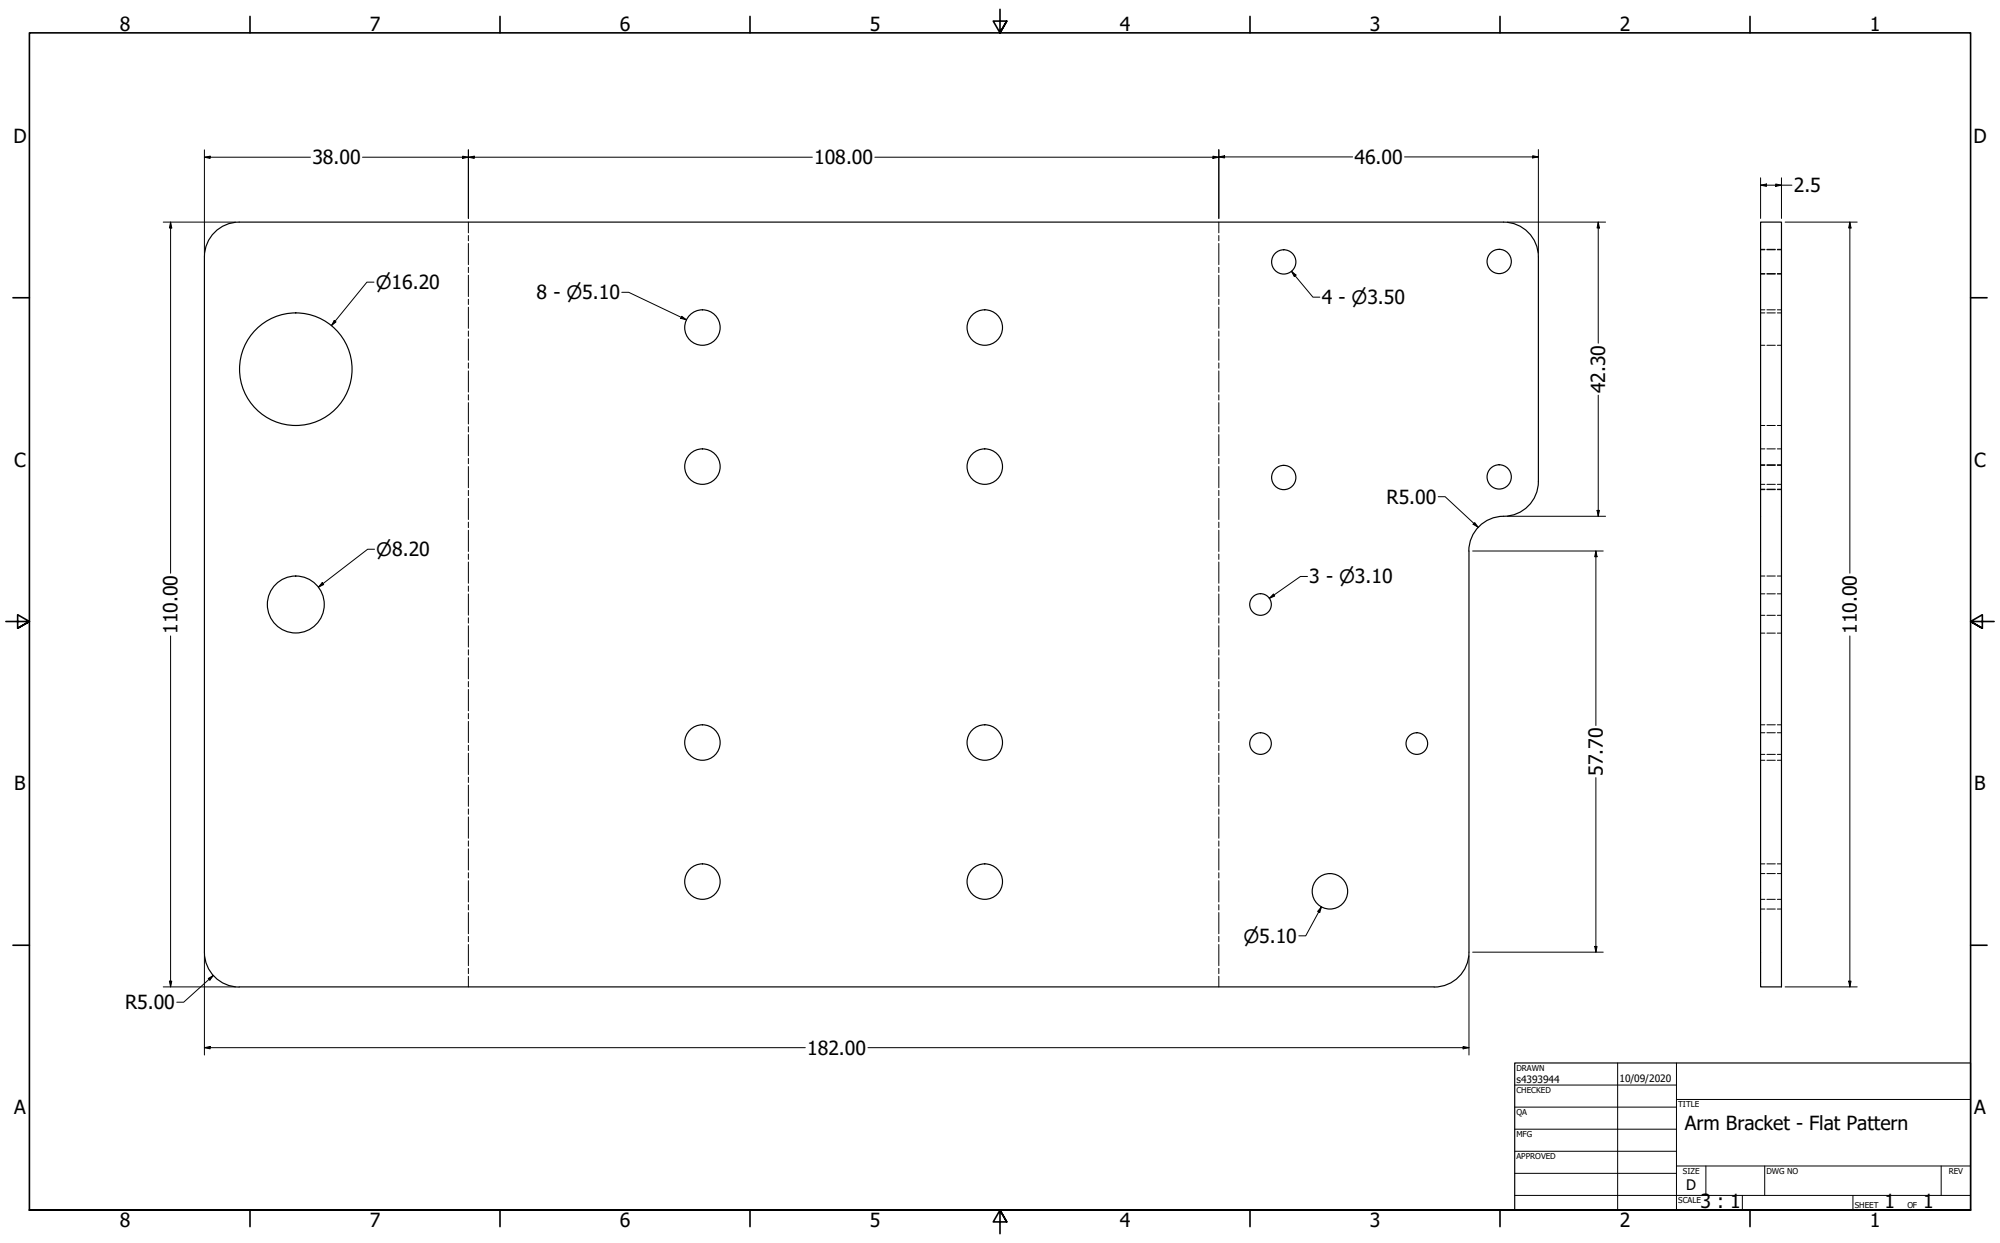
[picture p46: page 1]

DRAWN s4393944 | 10/09/2020

CHECKED

TITLE
Arm Bracket - Flat Pattern

MFG

APPROVED

SIZE D | DWG NO | REV

3 : 1 SCALE | | SHEET 1 OF 1

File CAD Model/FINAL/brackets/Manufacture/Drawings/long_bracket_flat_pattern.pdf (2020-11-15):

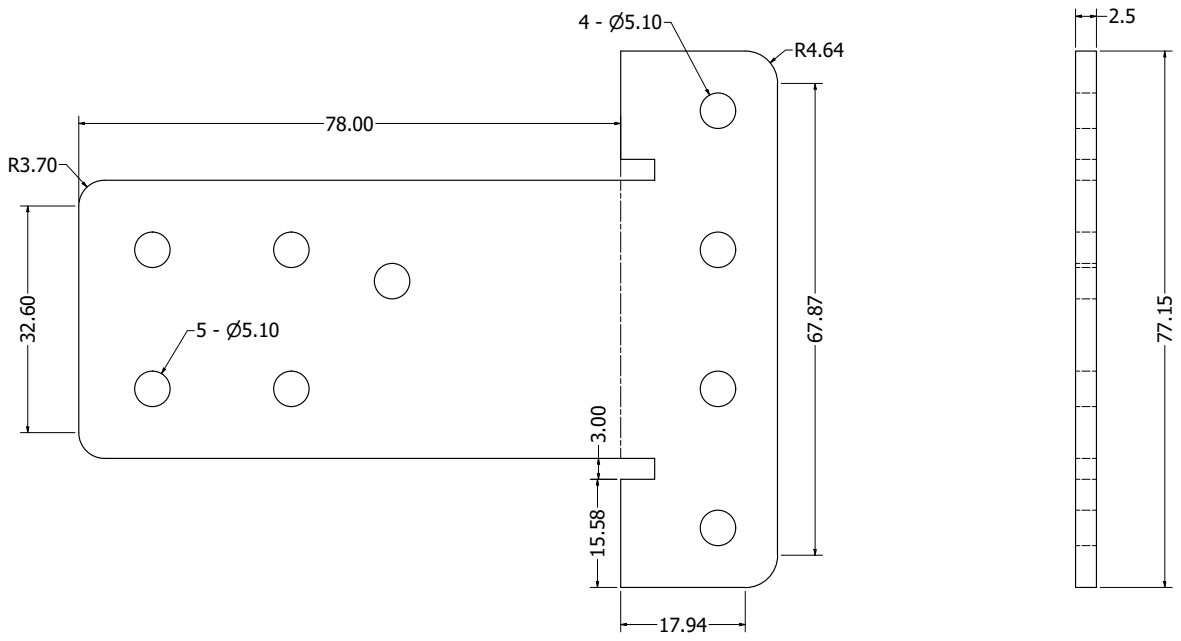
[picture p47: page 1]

DRAWN s4393944 | 10/09/2020

CHECKED

TITLE
Long Bracket - Folded

MFG

APPROVED

SIZE D | DWG NO | REV

3 : 1 SCALE | | SHEET 1 OF 1

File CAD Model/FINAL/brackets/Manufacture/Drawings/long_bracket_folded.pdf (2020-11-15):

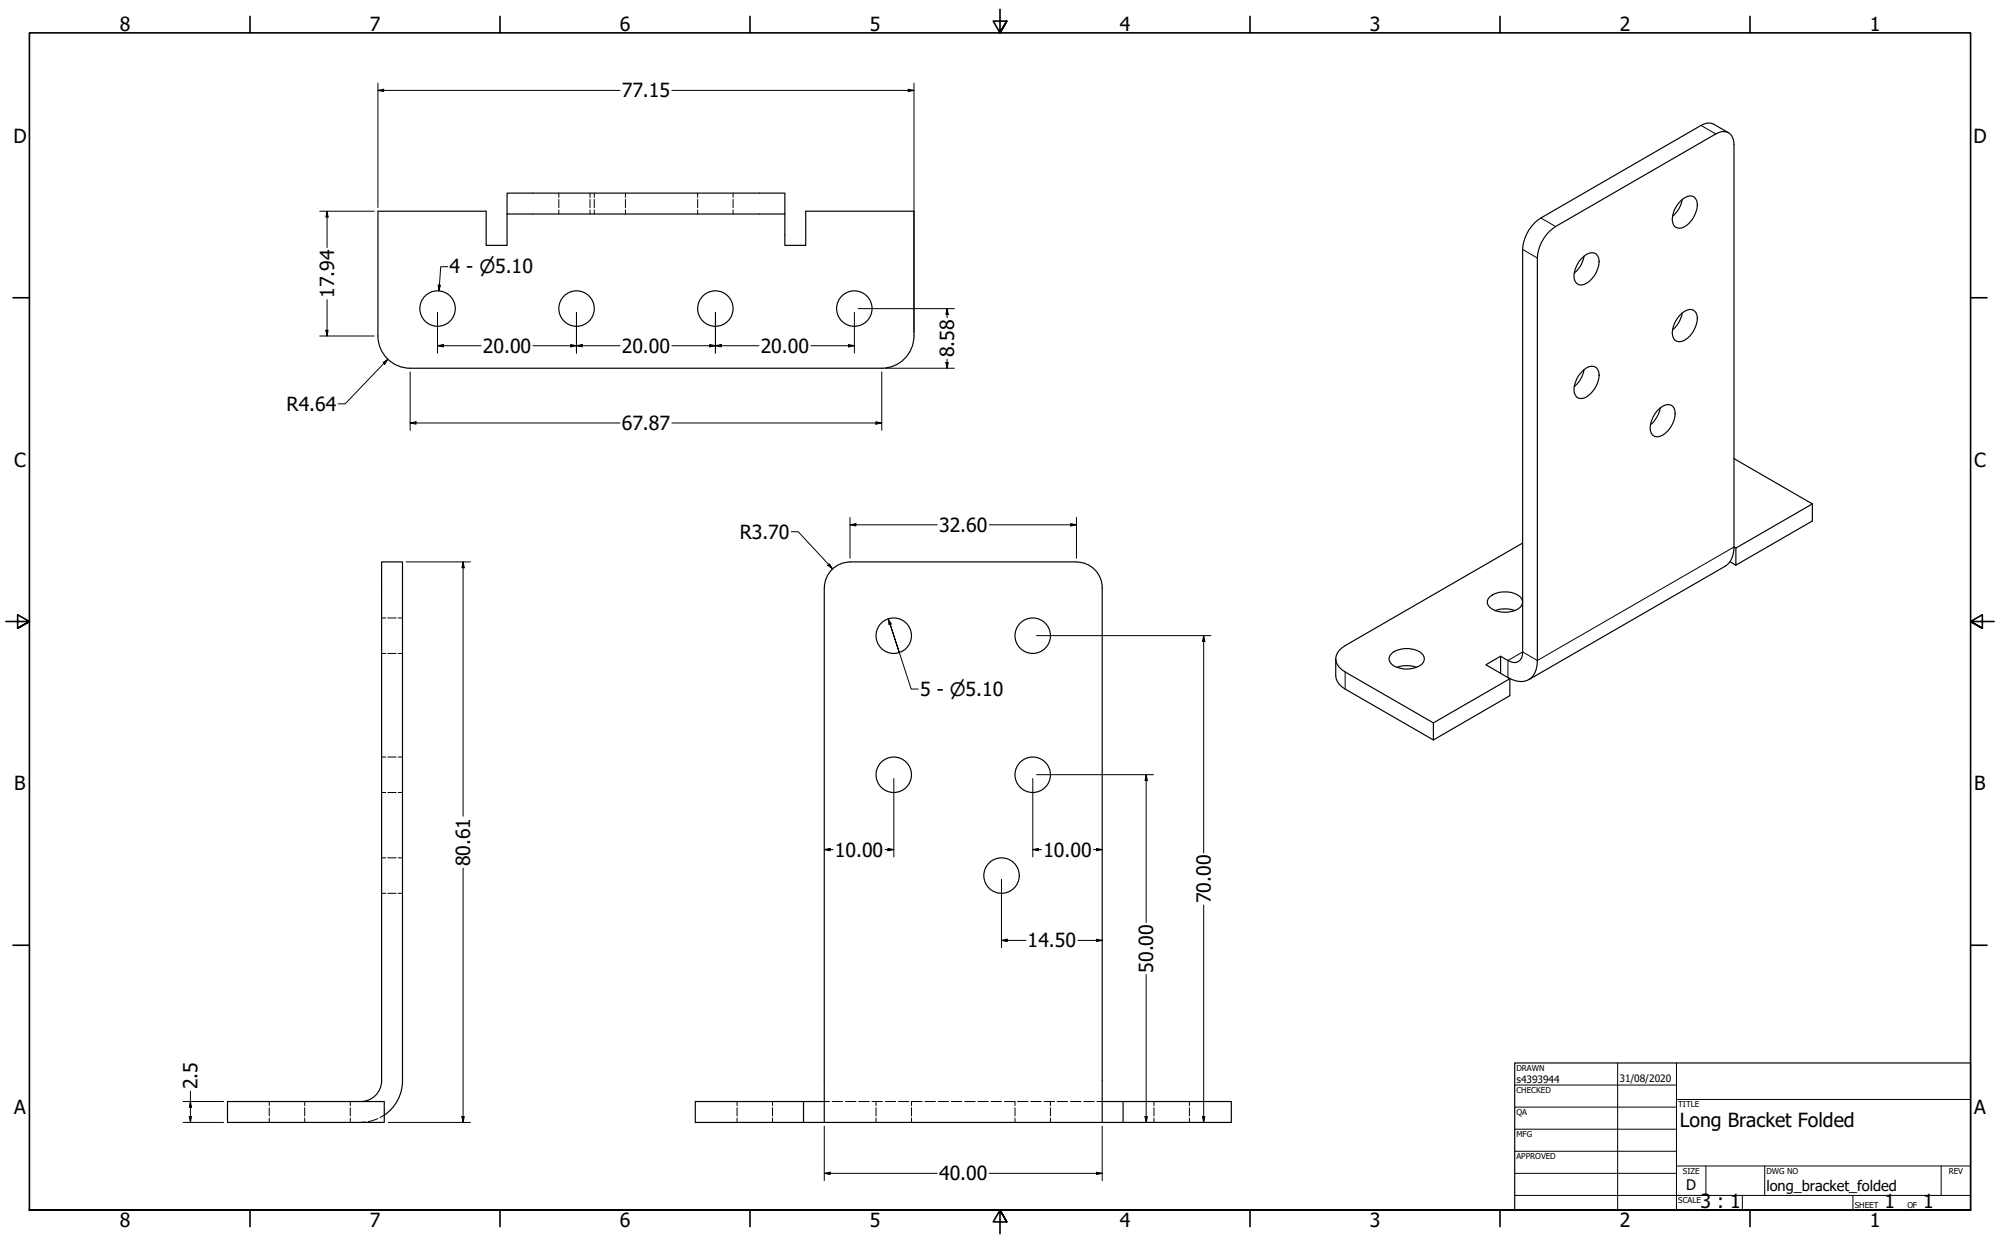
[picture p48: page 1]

DRAWN s4393944 | 31/08/2020

CHECKED

TITLE
Long Bracket Folded

MFG

APPROVED

SIZE D | DWG NO long_bracket_folded | REV

3 : 1 SCALE | | SHEET 1 OF 1

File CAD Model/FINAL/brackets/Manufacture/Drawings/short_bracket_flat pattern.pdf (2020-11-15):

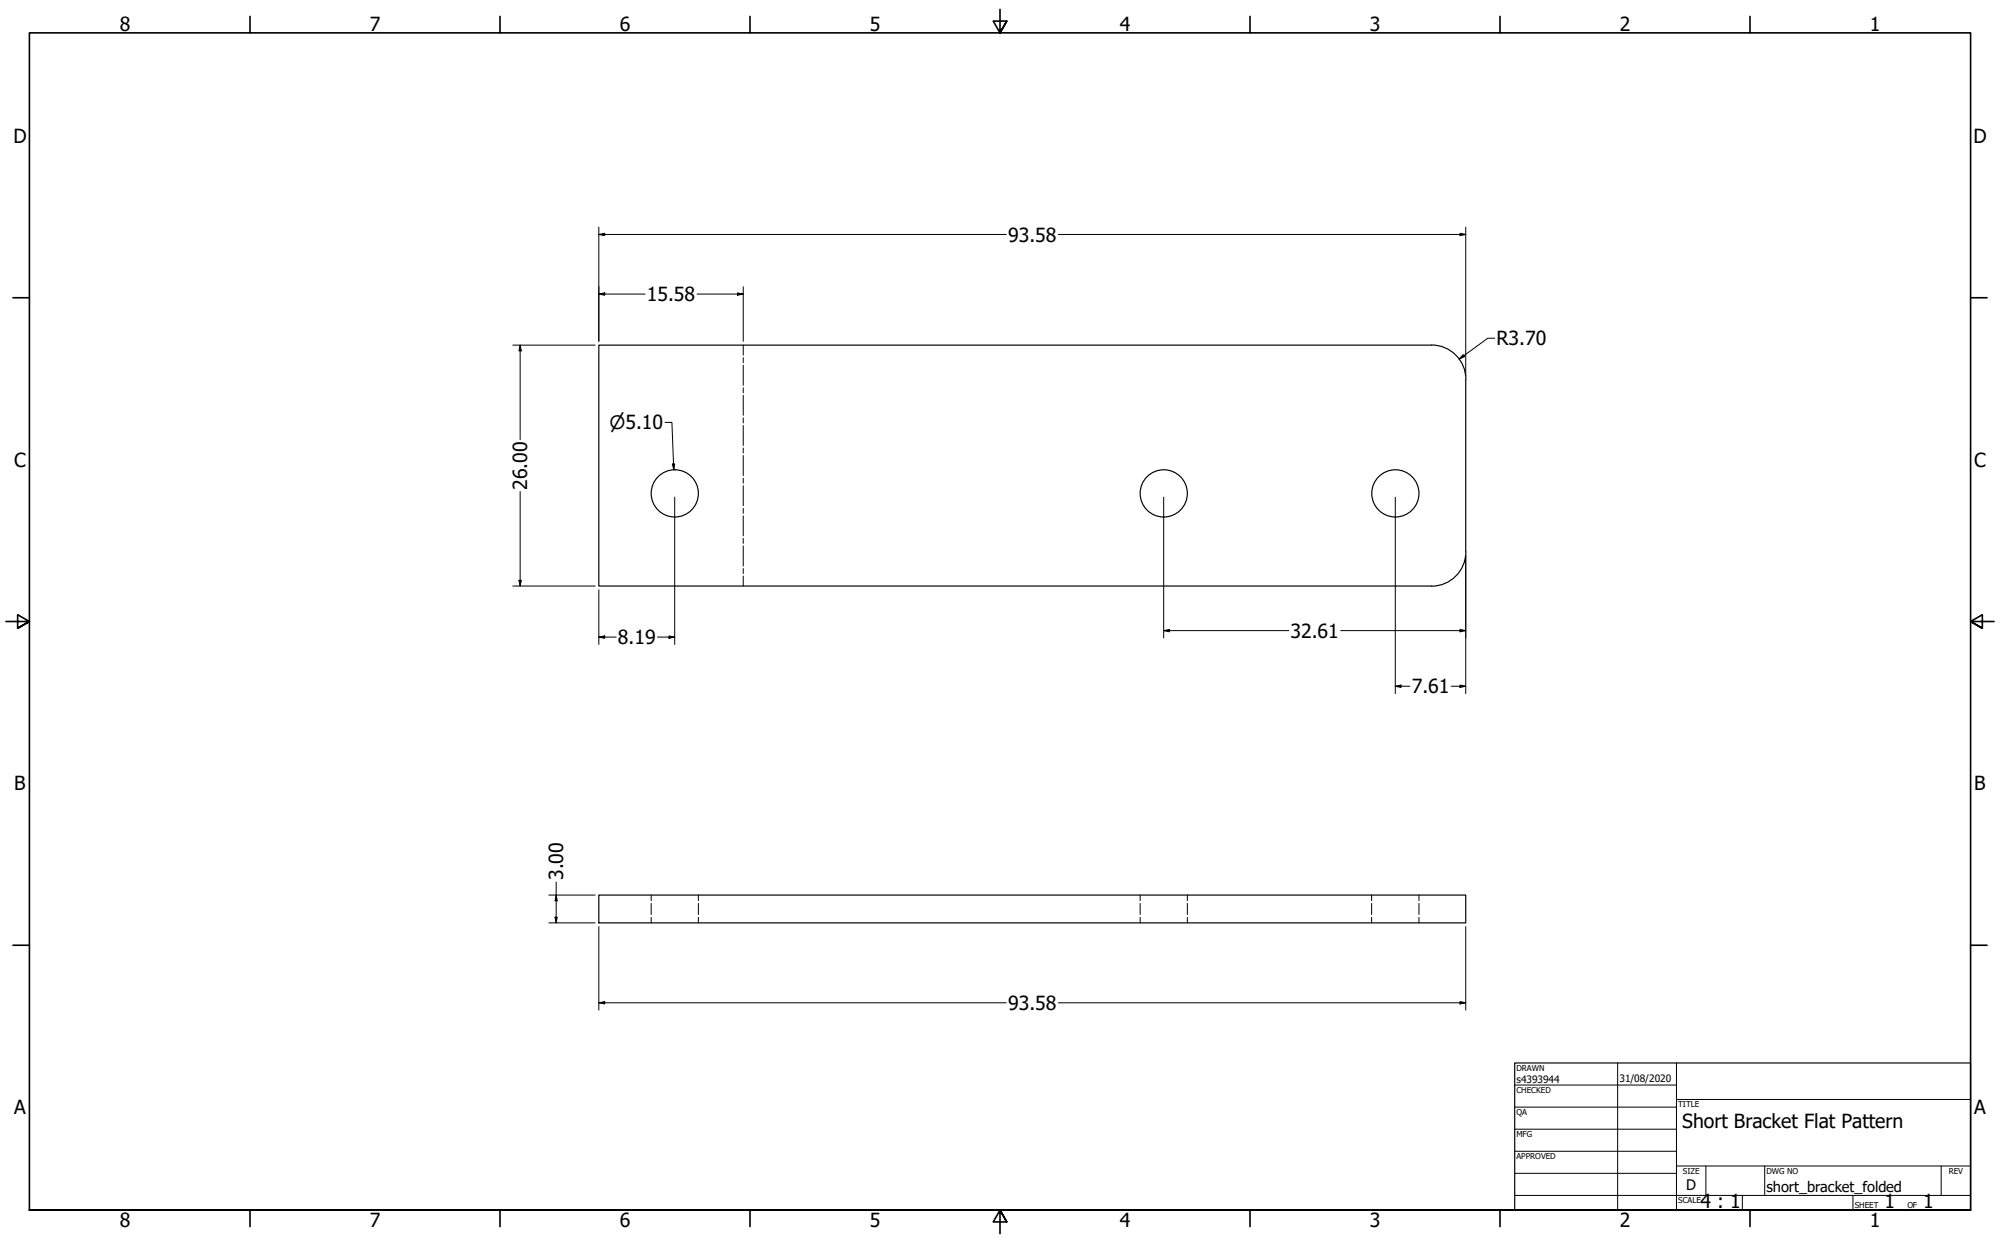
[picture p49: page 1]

DRAWN s4393944 | 31/08/2020

CHECKED

TITLE
Short Bracket Flat Pattern

MFG

APPROVED

SIZE D | DWG NO short_bracket_folded | REV

4 : 1 SCALE | | SHEET 1 OF 1

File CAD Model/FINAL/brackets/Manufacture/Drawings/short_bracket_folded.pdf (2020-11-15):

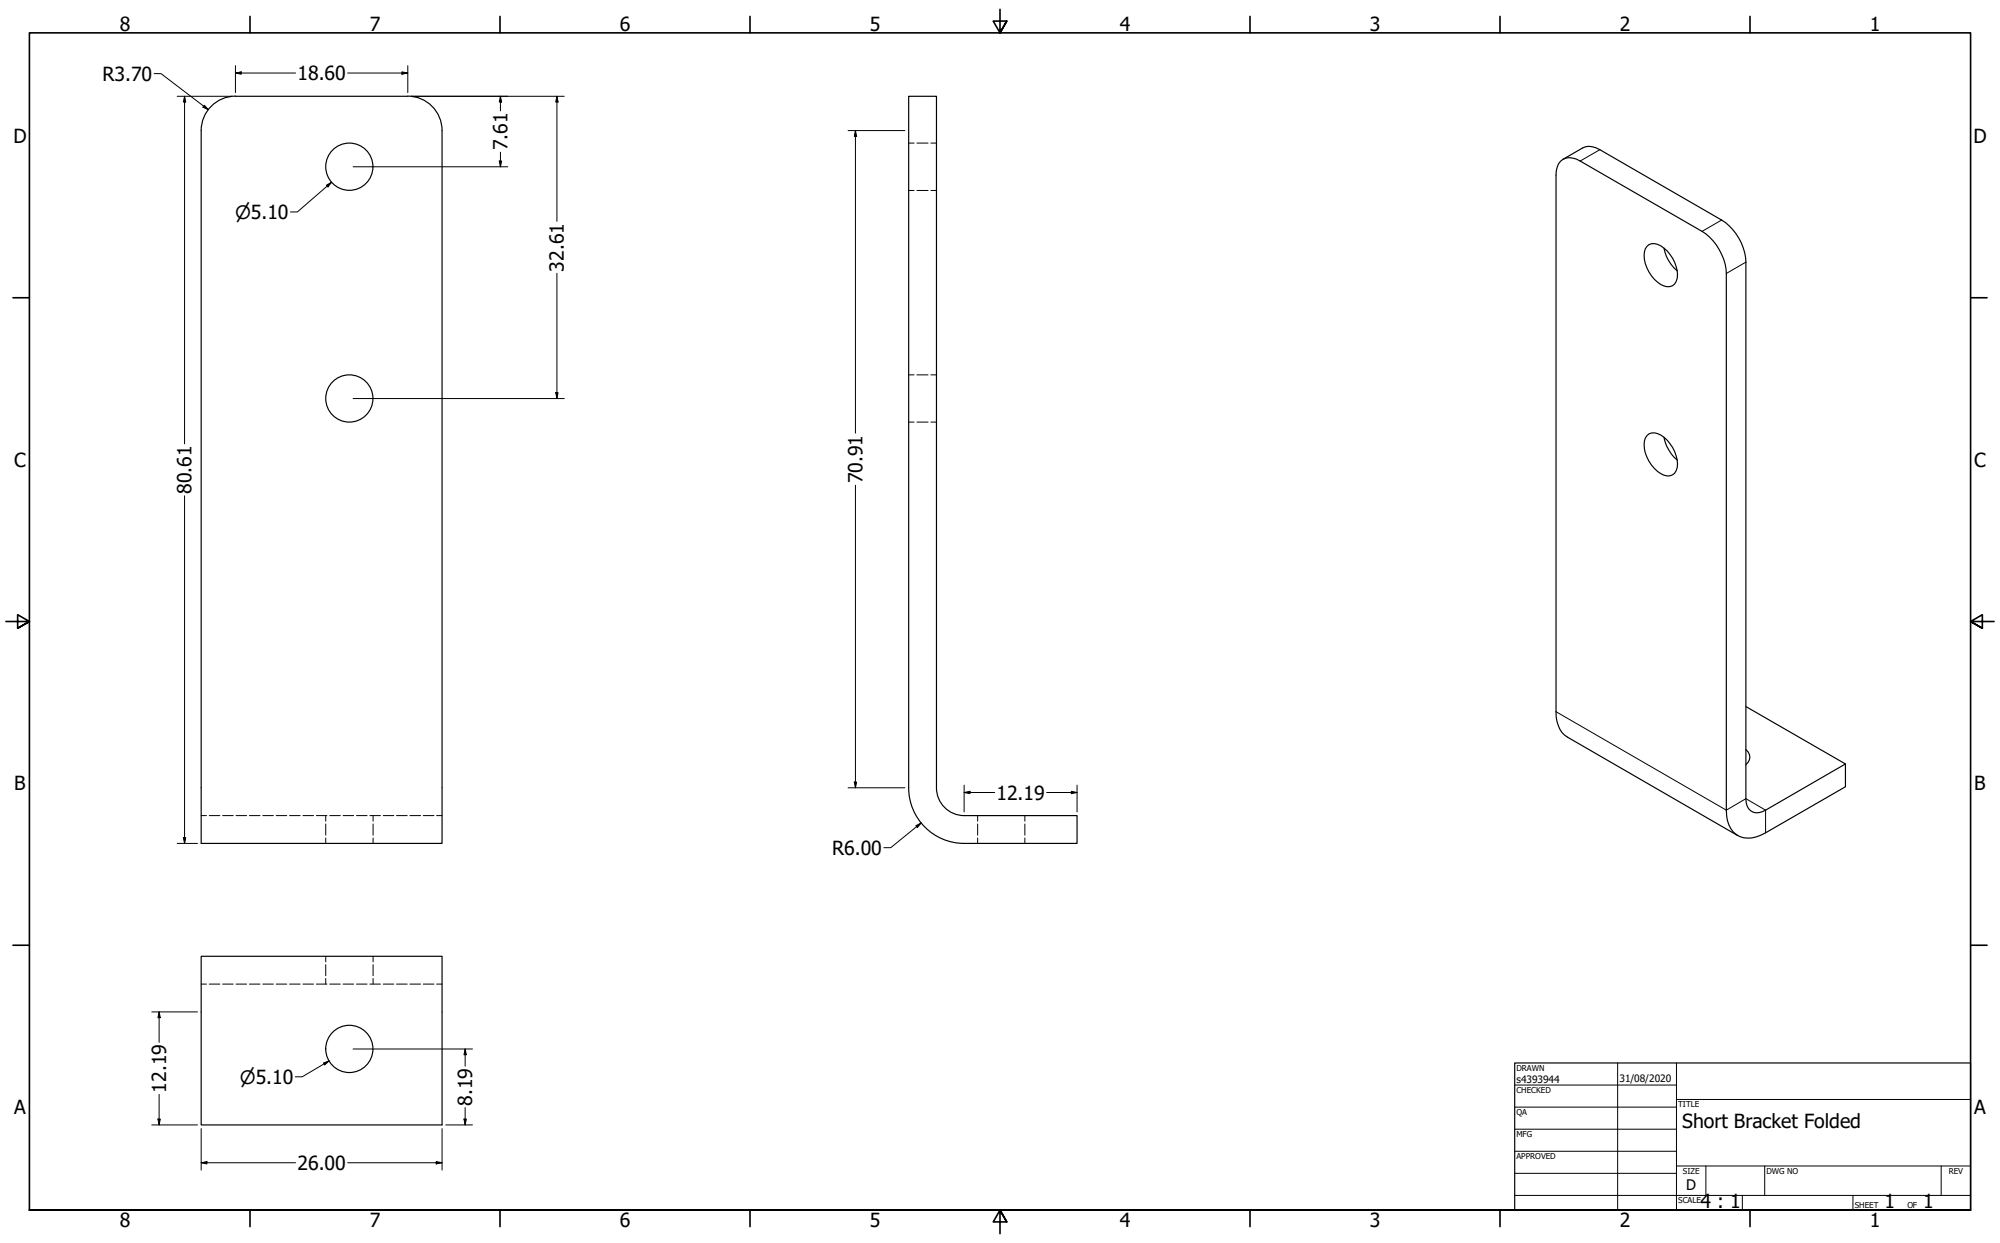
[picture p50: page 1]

DRAWN s4393944 | 31/08/2020

CHECKED

TITLE
Short Bracket Folded

MFG

APPROVED

SIZE D | DWG NO | REV

4 : 1 SCALE | | SHEET 1 OF 1

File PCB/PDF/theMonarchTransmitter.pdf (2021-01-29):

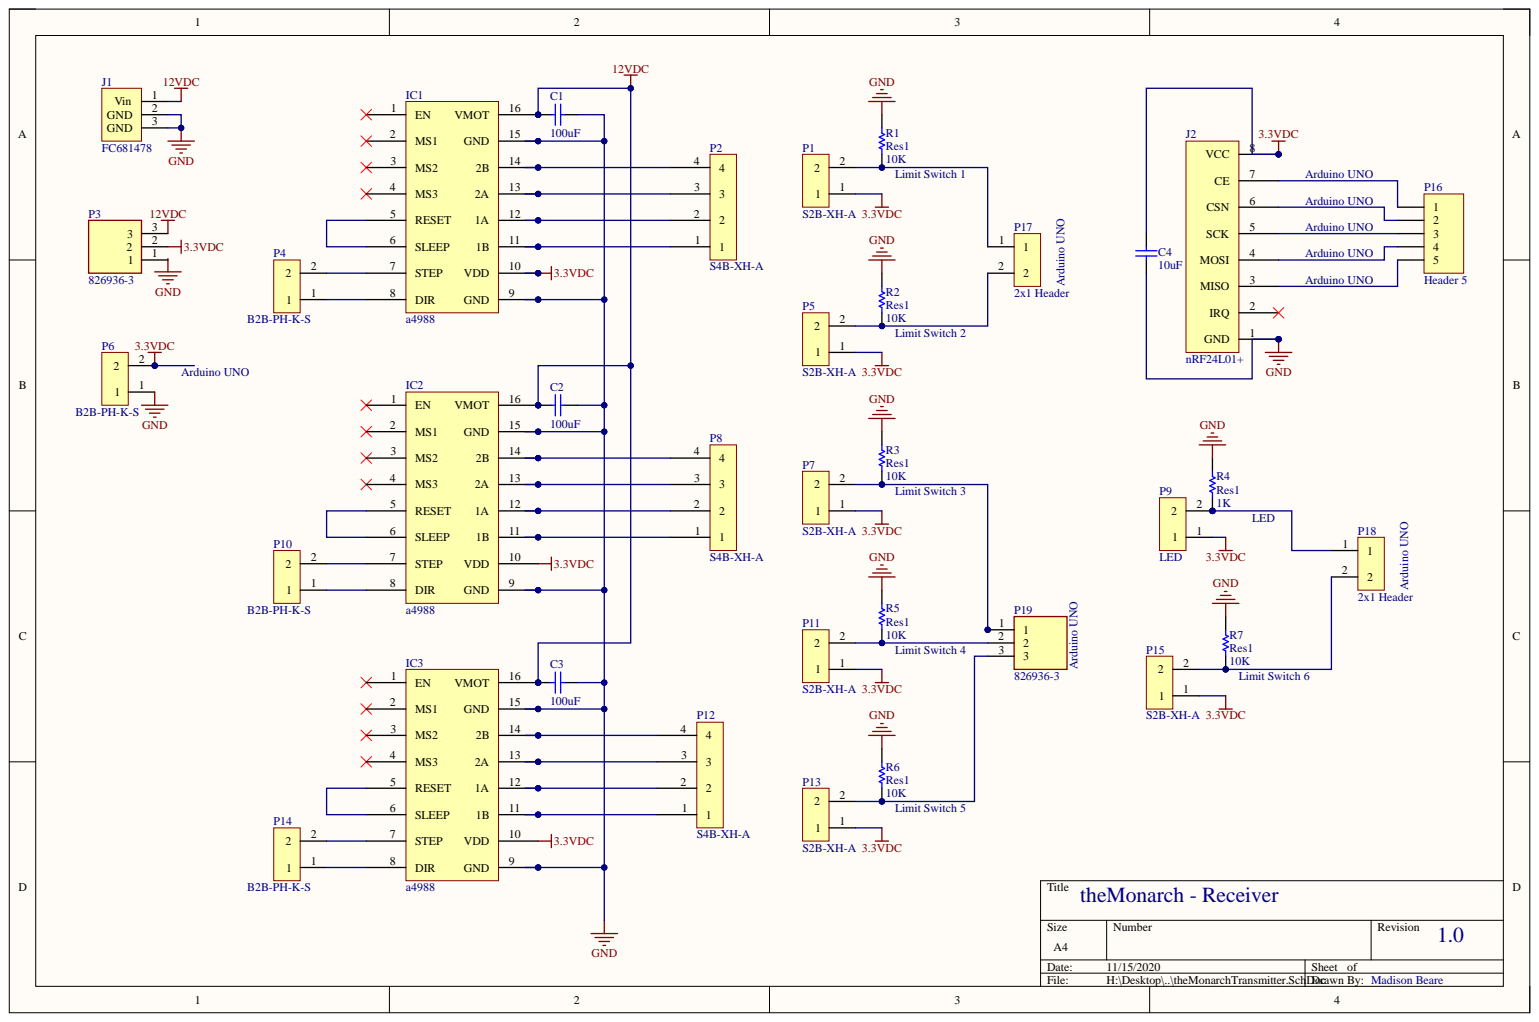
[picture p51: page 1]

Arduino UNO Arduino UNO Arduino UNO Arduino UNO Arduino UNO

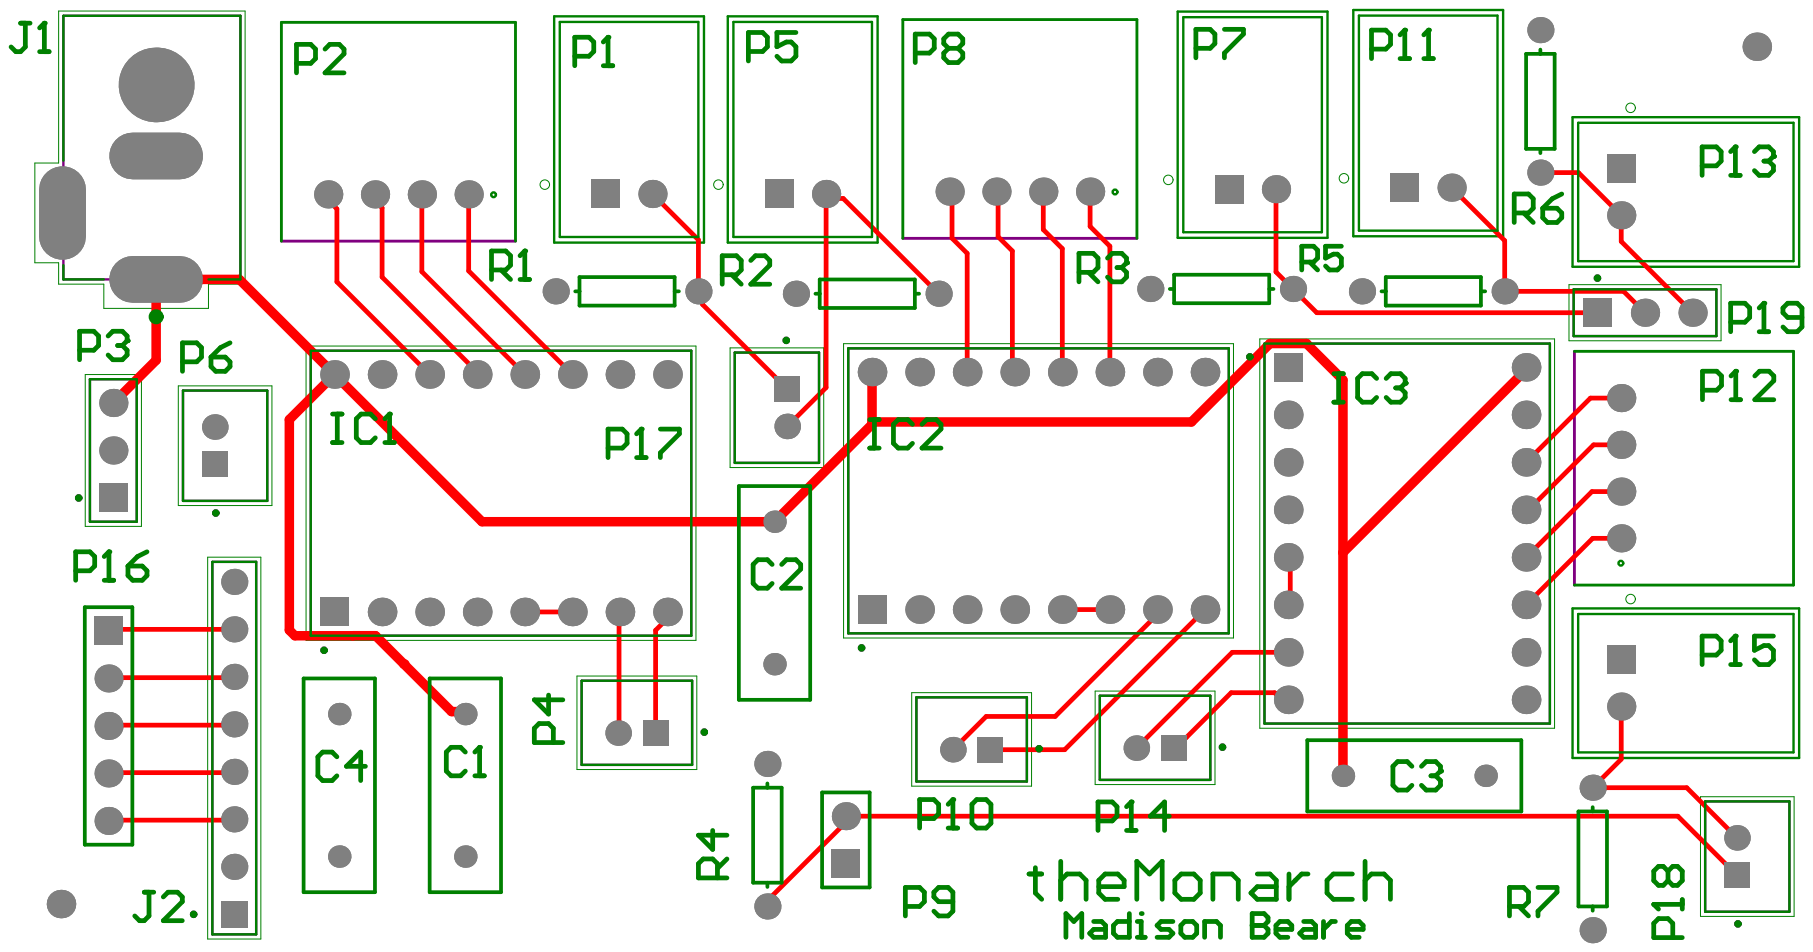
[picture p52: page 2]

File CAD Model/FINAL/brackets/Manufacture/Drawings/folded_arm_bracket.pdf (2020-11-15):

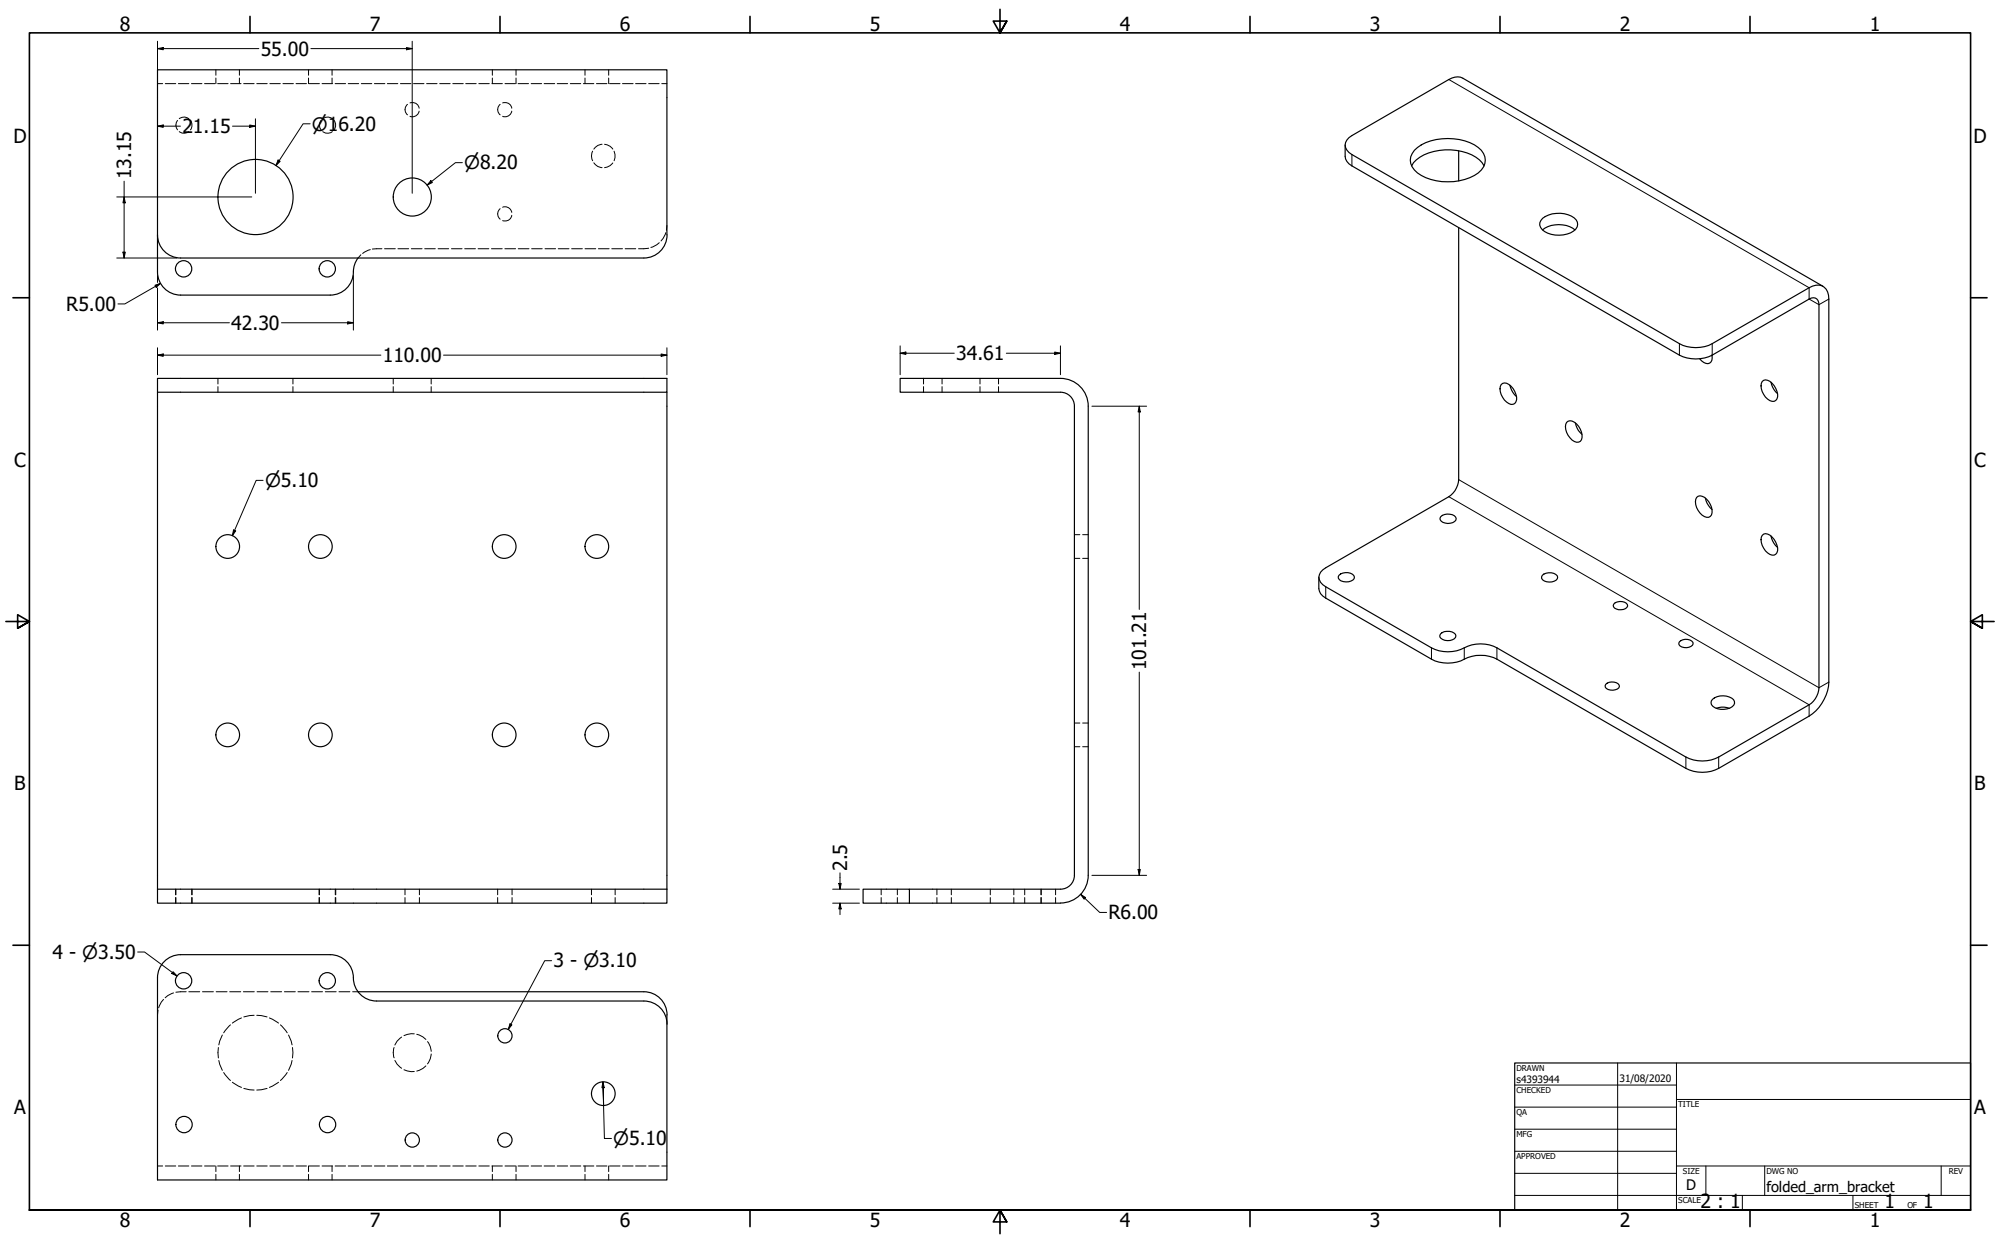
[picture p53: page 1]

DRAWN s4393944 | 31/08/2020

CHECKED

MFG

APPROVED

SIZE D | DWG NO folded_arm_bracket | REV

2 : 1 SCALE | | SHEET 1 OF 1

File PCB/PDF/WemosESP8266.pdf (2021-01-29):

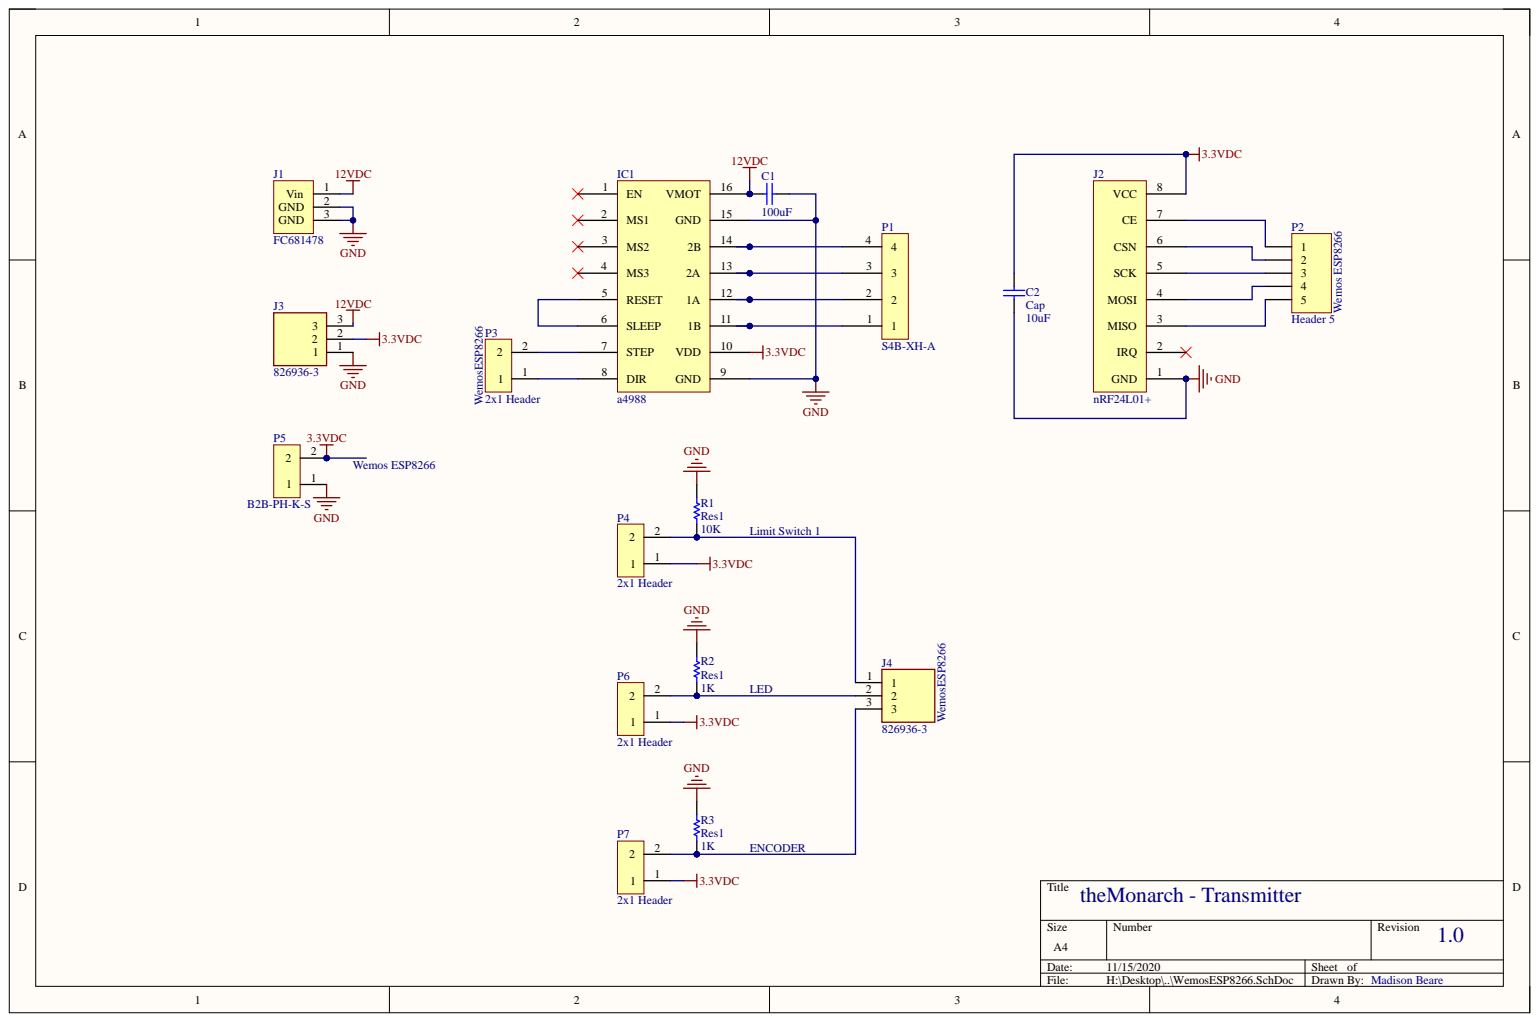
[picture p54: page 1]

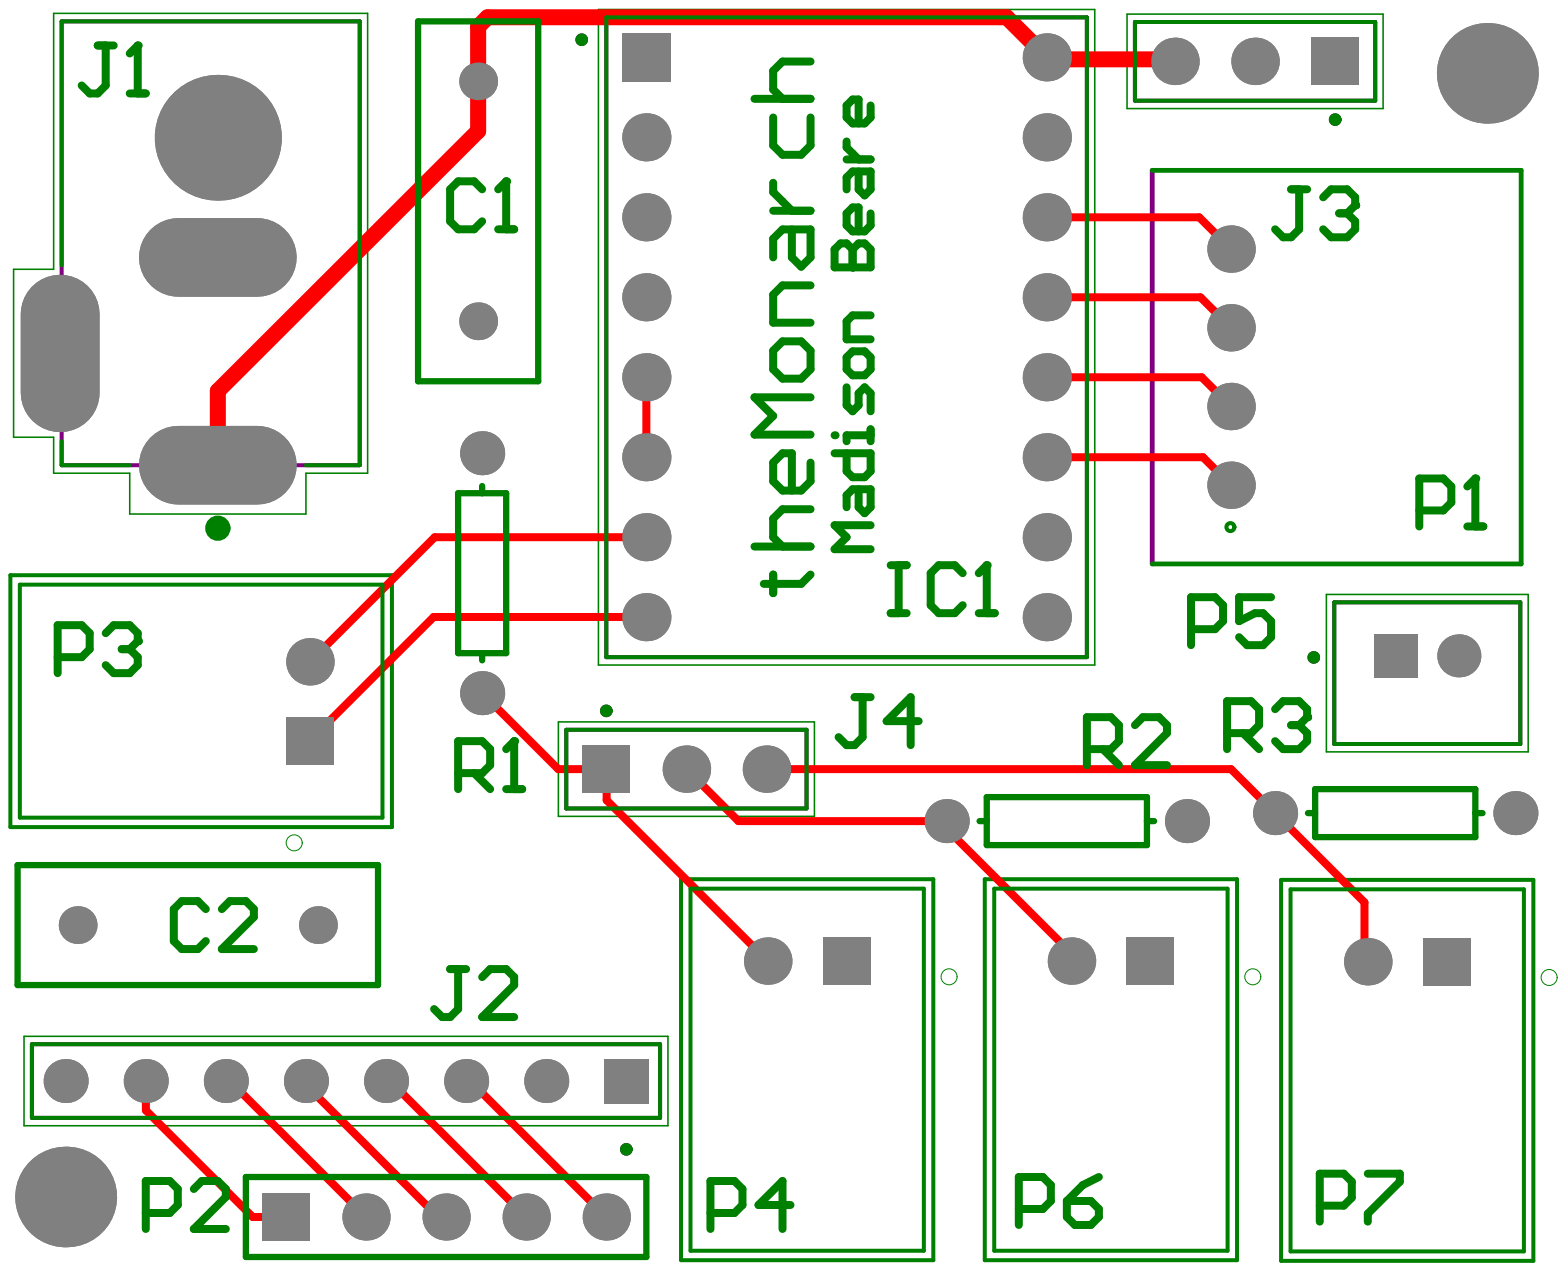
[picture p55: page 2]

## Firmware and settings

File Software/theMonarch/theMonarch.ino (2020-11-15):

#include <RadioHead.h>
#include <SPI.h>
#include <RH_nRF24.h>
#include <stdio.h>
#include <stdlib.h>

//---------------- RADIO FREQUENCY --------------------------
// Singleton instance of the radio driver
RH_NRF24 nrf24;

uint8_t buf[RH_NRF24_MAX_MESSAGE_LEN];
uint8_t len = sizeof(buf);
char coords[sizeof(buf)];
int i = 0;
bool check = false;

//---------------------------String Split----------------------
char shelf[sizeof(buf)];
char xcoord[sizeof(buf)];
char ycoord[sizeof(buf)];

int countX = 0;
int countY = 0;

int shelfNo;
int xCoords;
int yCoords;

//---------------- STEPPER MOTORS ----------------------------
// Define stepper motoor connections and steps per revolution
#define stepsPerRev 200

//LEAD SCREWS
//vertical lead screw
#define armLeadDIR 2
#define armLeadSTEP 3
//#define armDistanceTraversed y

//horizontal lead screw
#define cbeamLeadDIR 4
#define cbeamLeadSTEP 5
//#define cbeamDistanceTraversed x

//TIMING BELT
#define centreBeamDIR 6
#define centreBeamSTEP 7
//#define centreBeamDistanceTraversed z

//SWITHCES
#define armHomeSwitch A1
#define centreBeamHomeSwitch A2
#define cbeamHomeSwitch A3
#define centreBeamLimitSwitch A4
#define cbeamLimitSwitch A5

//calculations/setting distances
int armLeadSteps;
int cbeamLeadSteps;
int centreBeamSteps;

int stepsPerMM = 25;

//flags
bool centreBeamHomeFlag = false;
bool armHomeFlag = false;
bool cbeamHomeFlag = false;
bool centreBeamLimitFlag = false;
bool cbeamLimitFlag = false;

const int ledPin =  13;

//-------------------- SETUP -----------------------------
void setup() {
  Serial.begin(9600);

  //while (!Serial)
  ; // wait for serial port to connect. needed for Leonardo only
  if (!nrf24.init()) {
    Serial.print("init failed");
    // Defaults after init are 2.402 GHz (channel 2), 2Mbps, 0dBm
  }
  if (!nrf24.setChannel(1)) {
    Serial.println("setChannel failed");
  }
  if (!nrf24.setRF(RH_NRF24::DataRate2Mbps, RH_NRF24::TransmitPower0dBm)) {
    Serial.println("setRF failed");
  }

  // Declare output pins:
  pinMode(armLeadDIR, OUTPUT);
  pinMode(armLeadSTEP, OUTPUT);
  pinMode(cbeamLeadDIR, OUTPUT);
  pinMode(cbeamLeadSTEP, OUTPUT);
  pinMode(centreBeamDIR, OUTPUT);
  pinMode(centreBeamSTEP, OUTPUT);

  pinMode(armHomeSwitch, INPUT);
  pinMode(centreBeamHomeSwitch, INPUT);
  pinMode(cbeamHomeSwitch, INPUT);
  pinMode(centreBeamLimitSwitch, INPUT);
  pinMode(cbeamLimitSwitch, INPUT);

  pinMode(ledPin, OUTPUT);
}

//--------------------- LOOP -----------------------------

void loop() {

  delay(2000);

  while (!check) {
    receive();
  }

  homeAll(); 
  resetFlags(); 

  shelfNo = 1; 

  switch (shelfNo) {
    case 1:
      Serial.println("case 1"); 
      centreBeamUpMovement(960);
      break;
    case 2:
      Serial.println("case 2"); 
      centreBeamUpMovement(2300); 
      break; 
    case 3:
      Serial.println("case 3"); 
      centreBeamUpMovement(2955); 
      break; 
    default: 
      centreBeamUpMovement(1500); 
    }

    //ARM FULLY EXTENDED: 340MM
    //int horDistSteps = (pow((pow(xCoords,2) + pow(yCoords,2)),0.5) - 340)*25; 
    cbeamForwardMovement(600);
    
    delay(1000);

    armDownMovement(850); 

    homeAll(); 
    resetFlags(); 

    check = false; 

    while(1){
    }
}

//----------------------- CENTRE BEAM -----------------------------------

void centreBeamUpMovement(float centreBeamSteps) {
  // Set the spinning direction clockwise/upwards
  digitalWrite(centreBeamDIR, HIGH);

  // Spin the stepper motor _ revolutions slowly:
  for (int i = 0; i < centreBeamSteps; i++) {
    if (analogRead(centreBeamLimitSwitch) <= 255 && !centreBeamLimitFlag) {
      //The following result in 1 step:
      digitalWrite(centreBeamSTEP, HIGH);
      delayMicroseconds(4000);
      digitalWrite(centreBeamSTEP, LOW);
      delayMicroseconds(4000);
    } else {
      centreBeamLimitFlag = true;
      break;
    }
  }
  delay(1000);
}


void centreBeamDownMovement(float centreBeamSteps) {
  // Set the spinning direction anticlockwise/upwards
  digitalWrite(centreBeamDIR, LOW);

  // Spin the stepper motor _ revolutions slowly:
  for (int i = 0; i < centreBeamSteps; i++) {
    if (analogRead(centreBeamHomeSwitch) <= 255 && !centreBeamHomeFlag) {
      //The following result in 1 step:
      digitalWrite(centreBeamSTEP, HIGH);
      delayMicroseconds(4000);
      digitalWrite(centreBeamSTEP, LOW);
      delayMicroseconds(4000);
    } else {
      centreBeamHomeFlag = true;
      break;
    }
  }
  delay(1000);
}


//----------------------- C BEAM -----------------------------------
void cbeamForwardMovement(float cbeamLeadSteps) {
  // Set the spinning direction clockwise/fowards
  digitalWrite(cbeamLeadDIR, LOW);

  // Spin the stepper motor _ revolutions slowly:
  for (int i = 0; i < cbeamLeadSteps; i++) {
    if (analogRead(cbeamLimitSwitch) <= 255 && !cbeamLimitFlag) {
      digitalWrite(cbeamLeadSTEP, HIGH);
      delayMicroseconds(2000);
      digitalWrite(cbeamLeadSTEP, LOW);
      delayMicroseconds(2000);
    } else {
      cbeamLimitFlag = true;
      break;
    }
  }
  delay(1000);
}

void cbeamBackMovement(float cbeamLeadSteps) {
  // Set the spinning direction anticlockwise/backwards
  digitalWrite(cbeamLeadDIR, HIGH);

  // Spin the stepper motor _ revolutions slowly:
  for (int i = 0; i < cbeamLeadSteps; i++) {
    if (analogRead(cbeamHomeSwitch) <= 255 && !cbeamHomeFlag) {
      digitalWrite(cbeamLeadSTEP, HIGH);
      delayMicroseconds(2000);
      digitalWrite(cbeamLeadSTEP, LOW);
      delayMicroseconds(2000);
    } else {
      cbeamHomeFlag = true;
      break;
    }
  }
  delay(1000);
}


//----------------------- ARM -----------------------------------
void armUpMovement(float armLeadSteps) {
  // Set the spinning direction clockwise/fowards
  digitalWrite(armLeadDIR, LOW);

  // Spin the stepper motor _ revolutions slowly:
  for (int i = 0; i < armLeadSteps; i++) {
    if (analogRead(armHomeSwitch) <= 255 && !armHomeFlag) {
      //The following result in 1 step:
      digitalWrite(armLeadSTEP, HIGH);
      delayMicroseconds(6000);
      digitalWrite(armLeadSTEP, LOW);
      delayMicroseconds(6000);
    } else {
      armHomeFlag = true;
      break;
    }
  }
  delay(1000);
}

float armDownMovement(float armLeadSteps) {
  // Set the spinning direction clockwise/fowards
  digitalWrite(armLeadDIR, HIGH);

  // Spin the stepper motor _ revolutions slowly:
  for (int i = 0; i < armLeadSteps; i++) {
    //The following result in 1 step:
    digitalWrite(armLeadSTEP, HIGH);
    delayMicroseconds(5000);
    digitalWrite(armLeadSTEP, LOW);
    delayMicroseconds(5000);
  }

  delay(1000);
}


//----------------------- HOMING FUNCTIONS -----------------------------------
void homeCentreBeam() {
  // read the state of the limitswitch:
  while (!centreBeamHomeFlag) {
    centreBeamDownMovement(1000000);
  }
}

void homeCbeam() {
  while (!cbeamHomeFlag) {
    cbeamBackMovement(1000000);
  }
}

void homeArm() {
  // read the state of the limitswitch:
  while (!armHomeFlag) {
    armUpMovement(100000);
  }
}

void homeAll() {
  homeArm();
  homeCbeam();
  homeCentreBeam();
}

void resetFlags() {
  centreBeamHomeFlag = false;
  centreBeamLimitFlag = false;
  armHomeFlag = false;
  cbeamHomeFlag = false;
  cbeamLimitFlag = false;
}

//-------------------------- RECEIVER ------------------------------------------
void receive() {
  Serial.println("I am waiting for a message");
  uint8_t data[] = "yep";
  while (nrf24.waitAvailableTimeout(200) && nrf24.recv(buf, &len))
  {
    Serial.println("Something was received");

    for (i; i < sizeof(buf); i++)
    {
      coords[i] = buf[i];
      coords[i] = (char)buf[i];
      Serial.print(coords[i]);
    }

    //STRING SPLIT
    for (int j = 0; j < sizeof(coords); j++) {
      if (j < 1) {
        shelf[j] = coords[j];
        shelf[j] = (char)coords[j];
        shelfNo = atoi(shelf);
      }

      if (j >= 1 && j < 4) {
        xcoord[countX] = coords[j];
        xcoord[countX] = (char)coords[j];
        xCoords = atoi(xcoord);
        countX += 1;
      }

      if (j >= 4 && j < sizeof(coords)) {
        ycoord[countY] = coords[j];
        ycoord[countY] = (char)coords[j];
        yCoords = atoi(ycoord);
        countY += 1;
      }
    }
    Serial.println("SHELF =");
    Serial.println(shelfNo);
    Serial.println("XCOORDs =");
    Serial.println(xCoords);
    Serial.println("YCOORDs =");
    Serial.println(yCoords);
    Serial.println(coords);

    check = true;

    if (check == true) {
      while (i <= 50) {
        delay(1000);
        //sending data back now
        nrf24.send(data, sizeof(data));
        nrf24.waitPacketSent();
        Serial.println("something was sent");
        i++;
      }
    } break; 
  }
}

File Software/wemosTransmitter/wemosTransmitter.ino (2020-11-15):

//web connect
#include <ESP8266WiFi.h>
#include <SPI.h>            // For SPI comm (needed for not getting compile error)
#include <Wire.h>
WiFiClient client;

//transmitter
#include <RadioHead.h>
#include <SPI.h>
#include <RH_NRF24.h>
#include <stdio.h>
#include <stdlib.h>
#include <string.h>

//---------------------- TURNTABLE -------------------------
#define turnDIR 14 //(D5)
#define turnSTEP 12 //(D6)

#define turntableHomeSwitch 4

bool turntableHomeFlag = false;

float stepsPerDegree = 111.11;



//-----------------------------------------------------------
// Singleton instance of the radio driver
RH_NRF24 nrf24(2, 15);

int button = 4;
int buttonState = 0;

uint8_t buf[7];
uint8_t coords[7];
uint8_t len = sizeof(buf);
char confirm[sizeof(buf)];
uint8_t fin[sizeof(buf)];
int n;
bool check = false;
String message;

uint8_t data[sizeof(coords)];
int sendCount = 0;

String stayString = "\nWAITING";

char shelf[sizeof(buf)];
char xcoord[sizeof(buf)];
char ycoord[sizeof(buf)];

int countX = 0;
int countY = 0;

int shelfNo;
int xCoords;
int yCoords;


//--------------SSID of your Wi-Fi router && Password of your Wi-Fi router------------------------------
//const char* ssid = "Telstra1751";
//const char* password = "0819721227";
//const IPAddress server(192, 168, 15, 2);
//const int httpPort = 5000;

const char* ssid = "Madison's iPhone";
const char* password = "Madison1997";
const IPAddress server(172, 20, 10, 8);
const int httpPort = 5000;


//------------------------------------------------------------------------------------------------------
void setup() {
  pinMode(turnDIR, OUTPUT);
  pinMode(turnSTEP, OUTPUT);

  webConnectSetup();
  transmitSetup();
}

void loop() {
  delay(1000);
  sendGET();
  transmitLoop();
  //Add this when turntable works
  //  if (!message.equals(stayString)) {
  //    int rotationSteps = atan(yCoords/xCoords)*stepsPerDegree;
  //    homeTurntable();
  //    turntableHomeFlag = false;
  //
  //    turntableClockwiseMovement(rotationSteps);
//}
}

void sendGET() //client function to send/receive GET request data.
{
  if (client.connect(server, httpPort)) {
    Serial.println("Client Connected");
    client.println("GET /coords HTTP/1.1"); //download text
    client.println("Host: 192.168.15.2");
    client.println("Connection: close");  //close 1.1 persistent connection
    client.println(); //end of get request
  } else {
    Serial.println("connection failed"); //error message if no client connect
    Serial.println();
  }

  while (client.connected() && !client.available()) delay(1); //waits for data
  while (client.connected() || client.available()) { //connected or data available
    String line = client.readString();
    int contentBodyIndex = line.lastIndexOf('\n');
    if (contentBodyIndex > 0) {
      message = line.substring(contentBodyIndex);
      Serial.println("MESSAGE EQUALS =" + message);
      Serial.println(stayString);

      if (message.equals(stayString)) {
        Serial.println("EQUAL");
      } else {
        Serial.println("NOT EQUAL");
      }
      int messageIndex = 1;

      for (int i = 0; i < message.length() - 1; i++) {
        coords[i] = message.charAt(messageIndex);
        Serial.println();
        Serial.println(coords[i]);
        messageIndex += 1;
      }
      client.stop();
      client.flush();
    }
    
    shelfNo = 0; 
    countX = 0;
    countY = 0; 

    for (int j = 0; j < sizeof(coords); j++) {
      if (j < 1) {
        shelf[j] = coords[j];
        shelf[j] = (char)coords[j];
        shelfNo = atoi(shelf);

      }

      if (j >= 1 && j < 4) {
        xcoord[countX] = coords[j];
        xcoord[countX] = (char)coords[j];
        xCoords = atoi(xcoord);
        countX += 1;
      }

      if (j >= 4 && j < sizeof(coords)) {
        ycoord[countY] = coords[j];
        ycoord[countY] = (char)coords[j];
        yCoords = atoi(ycoord);
        countY += 1;
        
      }
    } 
  } 
  Serial.println(); 
  Serial.println(shelfNo); 
  Serial.println(xCoords); 
  Serial.println(yCoords); 
}

void webConnectSetup() {
  Serial.begin(9600);
  delay(10);

  Serial.println();
  Serial.print("Connecting to ");
  Serial.println(ssid);

  WiFi.begin(ssid, password);

  while (WiFi.status() != WL_CONNECTED) {
    delay(500);
    Serial.print(".");
  }
}

void transmitSetup() {
  Serial.begin(9600);
  pinMode(button, INPUT);

  if (!nrf24.init()) {
    Serial.println("init failed");
    // Defaults after init are 2.402 GHz (channel 2), 2Mbps, 0dBm
  }
  if (!nrf24.setChannel(1)) {
    Serial.println("setChannel failed");
  }
  if (!nrf24.setRF(RH_NRF24::DataRate2Mbps, RH_NRF24::TransmitPower0dBm)) {
    Serial.println("setRF failed");
  }
  Serial.println("I made it out of setup");
}

void transmitLoop() {
//  if (!message.equals(stayString) && !check && sendCount < 5 && digitalRead(button)){
if (digitalRead(button) && !check && sendCount < 5){
    nrf24.send(coords, sizeof(coords));
    nrf24.waitPacketSent();
    Serial.println("I am sending a message");
    sendCount += 1;
    return;
  } else {
    // Wait for a message
    Serial.println("I am waiting for a message");
    while (nrf24.waitAvailableTimeout(200) && nrf24.recv(buf, &len)) {
      //something was received
      Serial.println("Something was received");
      for (int i = 0; i < sizeof(buf); i++) {
        confirm[i] = buf[i];
        confirm[i] = (char)buf[i];

        n = atoi(confirm);
      }

      Serial.println(confirm);
      if (sizeof(confirm) == 7) {
        Serial.println("Acknowledgement Message Confirmed!");
        check = true;
        break;
      }
    }
  }
}

void homeTurntable() {
  // read the state of the limitswitch:
  while (!turntableHomeFlag) {
    turntableClockwiseMovement(1000000);
  }
}

void turntableCounterClockwiseMovement(float turnSteps) {
  // Set the spinning direction clockwise:
  digitalWrite(turnDIR, LOW);

  // Spin the stepper motor 1 revolution slowly:
  for (int i = 0; i < (turnSteps); i++) {
    if (!digitalRead(turntableHomeSwitch) && !turntableHomeFlag) {
      digitalWrite(turnSTEP, HIGH);
      delayMicroseconds(200000);
      digitalWrite(turnSTEP, LOW);
      delayMicroseconds(200000);
    } else {
      turntableHomeFlag = true;
      break;
    }
  }
  delay(1000);
}

void turntableClockwiseMovement(float turnSteps) {
  // Set the spinning direction clockwise:
  digitalWrite(turnDIR, HIGH);

  // Spin the stepper motor 1 revolution slowly:
  for (int i = 0; i < (turnSteps); i++) {
    digitalWrite(turnSTEP, HIGH);
    delayMicroseconds(200000);
    digitalWrite(turnSTEP, LOW);
    delayMicroseconds(200000);
  }
  delay(1000);
}

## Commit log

2020-11-15 Submission Components
    [100mm_v_slot_plate.dxf, 100mm_v_slot_plate.stp, Board.iam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]
2020-11-15 Submission Requirments
    [ElectricalBOM.xlsx, KBpcb01.PCBLIB, KBpcb02.PCBLIB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]
2020-11-15 submission finalised
    [10to1GearRatio.iam, 3mm_spacer.stp, 4to1Gear1.stl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]
2020-11-15 README updates
    [Nema 17 V Slot Belt Driven Actuator 500mm.stp, Nema17.stp, V-Slot Gantry Plate 20mm.step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]
